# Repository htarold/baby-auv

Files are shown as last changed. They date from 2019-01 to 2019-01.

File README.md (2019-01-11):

## What
Baby AUV is a low cost, open source micro AUV (autonomous
underwater vehicle) intended for environmental monitoring
applications.  Currently it has completed basic manoeuvring and
navigation tasks, and the payload sensors (CTD) is functioning.

To move forward, the project needs a real-world problem and a
domain expert to guide further development and to take the AUV
operational.  Contact me htarold@gmail.com if you think Baby AUV
can be useful for you, or if you are interested in working on
the project.  Ideally a community can be grown to handle the
development and operational issues.

At least initially, Baby AUV should be deployed in inland waters
free of current.  Ultimately, Baby AUV will be useable in
coastal waters.

You can see a clip of Baby AUV [here](https://www.youtube.com/watch?v=7lgA8mxeRek).

## Vital statistics
Length: 0.6m (1m including antenna)
Displacement: 3.5kg
Cost: BOM cost can probably be held down to USD500.
Depth: the thruster gland has been tested to 40m; the EC probe
is rated to 50m; the hull is probably good to a few hundred
metres.
Endurance: 48 hours
Speed: 2kt (this implies range is about 100 miles)
Vehicle sensors: GPS, compass, accelerometer, depth, odometer
(via propeller)
Payload sensors: electrical conductivity, temperature.
Other payloads can be added.
Communications: RF modem (434MHz).

## How Baby AUV is different
Unlike most AUVs, Baby AUV has no fins, and has only 1 thruster,
and a moving mass actuator (2 degrees of freedom).  But by keeping
it mechanically simple and therefore cheap, it has to employ
novel methods to turn.  Gross changes of direction are achieved by
stopping, pitching nose up (by moving its internals to the rear),
then slowly reversing the thruster.  While the vehicle slowly
descends, it also rolls about a vertical axis as it reacts to the
thruster torque. At the appropriate point, the thruster is stopped
and the AUV is pitched horizontal, pointing in a new direction.

While under way, small changes in heading are achieved by modulating
the torque to the propeller which has only one blade.  This tends to
walk the rear of the AUV slowly one way or the other.  Another way
to think about this is the asymmetry of the single bladed prop
causes the AUV to wobble slightly in normal use.  By appropriately
modulating it, the wobble can be biased more one way than the other.

It should also be clear that Baby AUV is capable of hovering.

Baby AUV depends on GPS for localisation.  This means that the
AUV must surface frequently in order to get a fix.
Conveniently, for most missions the surface is very close by.

Most AUV projects are first and foremost robotics projects.
By keeping *this* AUV simple, I hope to de-emphasise the robotics
aspect in order to let the data sampling take centre stage.  In a
sense, Baby AUV can be regarded as a self-propelled multiparameter
probe, where one of the sensors s replaced by a thruster.

## Missions

The relatively high endurance and long range makes it suitable
for prolonged monitoring missions.  The AUV visits the waypoints
indicated in a mission script, collecting data along the way.
There data are stored on the SD card, and are also opportunistically
broadcast when surfaced.  If out of radio range of "home base", any
other AUV or aerial drone in the area can copy this data to return
to the user.  (A [fountain code](https://en.wikipedia.org/wiki/Fountain_code) will be used to reduce the amount
of redundant data transmitted.)  Use of such data mules make data
available sooner, as well as extending the AUV's sampling domain.

Apart from using the CTD or other payload sensor, one novel use is
to employ the AUV itself as a hydrometric pendulum.  To do this, the
AUV is trimmed slightly negative (tending to sink instead of float),
and is parked on the bottom balancing on its nose.  Any current near
the bottom (not powerful enough to dislodge the AUV) will cause
the AUV to change pitch and heading like an upside down windsock;
these are picked up by the vehicle's compass and accelerometer.
This can provide a simple way to measure the bottom shear (e.g. for
sediment transport studies), which is otherwise expensive to measure.

Baby AUV's hovering capability can be used to turn it into a
self-deploying and self-recovering fixed depth Lagrangean drifter.

Baby AUV can be used in a high surface traffic area.  The small size,
low speed, and low cost means that the AUV will sacrificially lose
in any collision with another vessel.  Conveniently, when surfaced
the AUV will be vertical, which pose softens impacts.

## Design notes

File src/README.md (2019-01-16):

Wed 16 Jan 11:07:23 +08 2019

## Source directory

Development was done on a Linux host using avr-gcc and avr-libc.
The target was flashed with the Arduino bootloader, but the
Arduino environment was not used anywhere else.  The Makefile
reflects this environment.  It's probably possible to develop on
a Windows rather than Linux host.

The binaries prefixed with `test_` are single threaded executables.
Most of them are for testing various aspects of the AUV on the
bench, including calibration.

The binaries prefixed with `tasks_` are cooperatively multitasking
executables, generally used for tank and field testing.

The multitasking consists of a simple round robin scheduler.
There are 3 hard-coded tasks: after `main()` is called, it turns
into the idle task; there is also a foreground task and a
background task.  The 3 tasks nominally take 10ms to execute in
total, the idle task soaking up any excess time to make up the
10ms.  In practice this is often the case, but nothing bad
happens if a task takes too much timer.

A task calls `yield()` to pass execution to the next task.  A
task must NOT `return`.  Extra tasks cannot be spawned, and
tasks are not allowed to die.  `yield()` can be used to delay
for approximately 10ms.

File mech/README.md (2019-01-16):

Wed 16 Jan 11:31:11 +08 2019

## Mechanical drawings

These 2D drawings were done on librecad.
I still need to properly annotate these drawings.

### `antenna.dxf`
This is for the antenna radome.  The radome contains 2 antennas
proper, for GPS and 433MHz modem.  A CNC
router (or you can use a milling machine) is used to rout out
the pocket and outline out of PVC.  Then a lathe is used to turn the
nipple, the 433MHz section, and to drill the holes for the
433MHz spring and nipple.  You may be able to get by with using
a drill press for this but it's rather dangerous.

The GPS antenna is an off-the-shelf active small ceramic patch
antenna.  The tiny screening
can over the LNA needs to be removed in order to replace the IPX
coax cable with a longer one (the can being replaced after that).
The coax cable _must be threaded_ through the antenna radome before
this is done!  Similarly for the 433MHz coax cable.  Note the
433MHz spring coax cable must be routed _behind_ the GPS antenna,
so that it lies against the screen can of the LNA, and the GPS
patch antenna must be installed facing the pocket opening.
Then the radome caps can be cemented in place with PVC cement.
You can the do the leak test.

### `baby.dxf`
Main drawing for all parts associated with the hull assembly.

The bulkhead sealing deserves a few words.  The two bulkheads take
a Neoprene ring of 5-6mm square cross section, which is compressed
against the hull by the 6 M4 screws.  This makes a water tight seal,
and also firmly attaches the bulkhead to the hull, obviating the
need for screws.  The Neoprene ring is made from a strip of the
appropriate length, by gluing the ends together in the same way
that O-rings can be made from O-ring cord.  My old source for
Neoprene strip has disappeared and I haven't looked for a new
one, but Neoprene from any source can be used.

The bulkheads themselves are turned on a lathe.  Most machining
work is concentrated here.

Small brackets are generally made from aluminium angle stock.

### `tracker.dxf`
Parts for the GPS tracker.

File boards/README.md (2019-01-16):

Wed 16 Jan 10:42:28 +08 2019

## Printed circuit boards

Baby AUV uses these PCBs.

Schematic capture and layout were done on gschem (*.sch files) and pcb
(*.pcb files) respectively, of the gEDA package.  The .tgz files
contains these, as well as the board-house-ready Gerbers.  AFAIK
these applications do not run on Windows.  The *.sch files are
NOT Eagle files.

For convenience, the *.sch.pdf (board schematics) files are also
included in the tar file.

The Makefile is only used to prepare the tgz files for upload.

### bat.{sch,pcb}
A small board to tie the 2 batteries in parallel; also
used for charging the batteries.

### encode.{sch,pcb}
This small board also doubles as the mounting for
the thruster motor.  The encoder uses an IR reflective sensor
pointed at the top surface of the shaft coupler, half of which
is coloured black with a permanent marker.  This marking must be
properly synced, so that as the prop blade rises, the encoder
outputs a rising edge, and when the blade falls, it outputs a
falling edge.

### mpx5700-pcb.{sch,pcb}
This carries the MPX5700 pressure sensor, and attaches to the
aft bulkhead.

### neo6m-hc12.{sch,pcb}
This board carries the GPS module and RF modem module, and mounts
to the foward bulkhead.  It also carries an I2C port expander to
multiplex the UARTs of both modules, as well as power them on
and off.  This board does not strictly conform to the pf-
interface.

### pf-ec.{sch,pcb}
The CTD board, which takes input from the MPX500 depth
sensor and elecrical conductivity probe.  The pf-* boards all conform
to the same IDC bus and mechanical interface.

### pf-mcu.{sch,pcb}
The MCU (ATmega328p) board.  This also carries the DC-DC
converter and servo interface (for the moving mass actuator).

### pf-thruster.{sch,pcb}
The thruster board.  This interfaces to the
thruster, which is a DC motor, and the encoder board.

### tracker-power.{sch,pcb}
This is only used in the RF tracker, not the
AUV.  It is a mounting for the battery socket, switch, and
charging board.

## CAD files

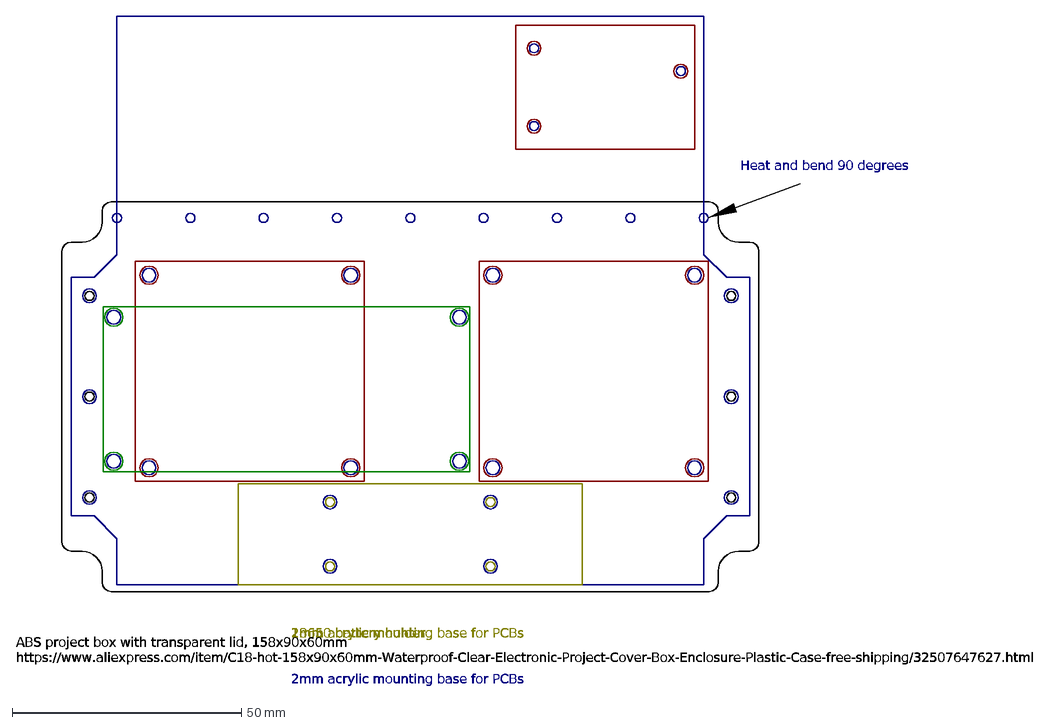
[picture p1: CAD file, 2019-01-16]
mech/tracker.dxf
18650 battery holder
2mm acrylic mounting base for PCBs
Heat and bend 90 degrees
ABS project box with transparent lid, 158x90x60mm https://www.aliexpress.com/item/C18-hot-158x90x60mm-Waterproof-Clear-Electronic-Project-Cover-Box-Enclosure-Pl

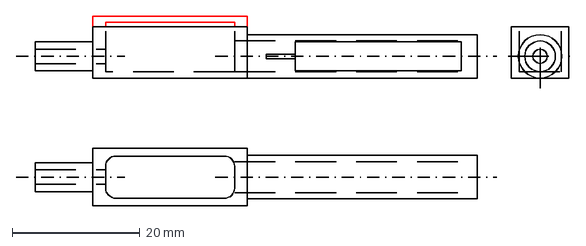
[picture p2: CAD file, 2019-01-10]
mech/antenna.dxf
86.6 x 29.7 mm

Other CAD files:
mech/baby.dxf

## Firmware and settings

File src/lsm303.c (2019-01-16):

/*
  (C) 2019 Harold Tay LGPLv3
  LSM303:
  Accel gives 12 bit values, but range is +/-2g, so 1g
  corresponds to 1024.
  Bits are LEFT aligned.

  For orientation, follow Table 2 of LSM app note:
               Ax Ay Az
  Z down       0  0  +1g
  Z up         0  0  -1g
  Y down       0 +1g 0
  Y up         0 -1g 0
  X down      +1g 0  0
  X up        -1g 0  0
  These are the axes of the AUV, XYZ are NED.  Change the
  AUVXFRONT/AUVYLEFT/AUVZUP macros in tude.h until the a[]
  values have the correct sign.

  Compass REQUIRES calibration; Z axis is generally badly off.
  Compass gain should also not be max because the values may
  overflow before applying the calibration offsets.
 */

#include <avr/eeprom.h>
#include "i2c.h"
#include "tude.h"
#include "tx.h"
#include "fmt.h"
#include "ee.h"                       /* for calibration values */

#define LSM303DLHC

#undef  DBG_LSM303
#ifdef DBG_LSM303
#define PRINT(a) a
#else
#define PRINT(a) /* nothing */
#endif

static struct tude calib;  /* contains calibration offsets */

static int8_t load_offsets(int16_t * ary, int16_t * addr)
{
  if (ee_load(ary, addr, sizeof(calib.cmpas_offsets))) {
    uint8_t i;
    for(i = 0; i < 3; i++) ary[i] = 0;
    /* is uncalibrated, calibration is REQUIRED */
    return(1);
  }
  return(0);
}

/*
  Accelerometer addresses are different for DLH and DLHC.
 */
#define ACCEL_ADDR_DLH (0x18<<1)
#define ACCEL_ADDR_DLHC (0x19<<1)
#define CMPAS_ADDR (0x1E<<1)
static uint8_t accel_addr;

static int8_t accelinit(int8_t addr)
{
  int8_t e;

  i2c_init();
  if( (e = i2c_setreg(addr, 0x20, 0x37)) )return(e);
  /* CANNOT set small/native endian, DLHC bug. */
  e = i2c_setreg(addr, 0x23, addr == ACCEL_ADDR_DLHC?0x1:0);
  return(e);
}
int8_t accel_init(void)
{
  int8_t e;
  e = accelinit(accel_addr = ACCEL_ADDR_DLH);
  if (e) e = accelinit(accel_addr = ACCEL_ADDR_DLHC);
  if (e) return(e);
  return(load_offsets(calib.accel_offsets, ee.tude.accel_offsets));
}
static void reorient(int16_t ary[3])
{
  int16_t tmp[3];
  tmp[0] = AUVXFRONT(ary);
  tmp[1] = AUVYRIGHT(ary);
  tmp[2] = AUVZDOWN(ary);

  ary[0] = tmp[0];
  ary[1] = tmp[1];
  ary[2] = tmp[2];
}
static int8_t read6(uint8_t addr, uint8_t reg, uint16_t ary[3])
{
  int i;
  uint8_t buf[6];
  i = i2c_read(addr, reg, buf, 6);
  if( i )return(i);
  for(i = 0; i < 3; i++) {
    ary[i] = (buf[(i*2)]<<8) | (buf[(i*2)+1] & 0xff);
  }
  return(0);
}

int8_t accel_read_raw(int16_t ary[3])
{
  int8_t e;
  uint16_t tmp[3];
#define AUTO_INCREMENT (1<<7)
  e = read6(accel_addr, 0x28|AUTO_INCREMENT, tmp);
  if( e )return(e);
  /* convert endian (accel only) */
  ary[0] = ((tmp[0] << 8) & 0xff00) | ((tmp[0] >> 8) & 0xff);
  ary[1] = ((tmp[1] << 8) & 0xff00) | ((tmp[1] >> 8) & 0xff);
  ary[2] = ((tmp[2] << 8) & 0xff00) | ((tmp[2] >> 8) & 0xff);
  ary[0] /= 16;
  ary[1] /= 16;
  ary[2] /= 16;
  return(0);
}

int8_t check_magnitude(uint16_t nom2, int16_t ary[3])
{
  uint16_t magnitude2;
  uint8_t i;
  magnitude2 = (ary[0]/8)*(ary[0]/8)
             + (ary[1]/8)*(ary[1]/8)
             + (ary[2]/8)*(ary[2]/8);
  if( magnitude2 > nom2 )magnitude2 -= nom2;
  else magnitude2 = nom2 - magnitude2;
  nom2 -= nom2/4;
  for(i = 0; i < 8; i++){
    if( magnitude2 >= nom2 )break;
    magnitude2 <<= 1;
  }
  return(i);
}
int8_t accel_read(int16_t ary[3])
{
  int8_t e, i;
  e = accel_read_raw(ary);
  if( e )return(e);
  for(i = 0; i < 3; i++){
    ary[i] += calib.accel_offsets[i];
  }
  reorient(ary);
#if 0
  /*
    Warn if acceleration != 1g.
    Scaled so that 1g = 1024/8 = 128
    Compare the square: should be close to 128*128 = 16384
   */
  return(check_magnitude(16384, ary));
#else
  return(0);
#endif
}

static uint8_t cmpas_xzy;

int8_t cmpas_init(void)
{
  int8_t e;
  uint8_t b;

  /*
    Compass gain max = 1<<5, min = 7<<5
   */
  i2c_init();
  PRINT(tx_puts("## setreg 1...\r\n"));
  if( (e = i2c_setreg(CMPAS_ADDR, 0x00, 0x14)) )return(e); /* 30Hz */
  PRINT(tx_puts("## setreg 2...\r\n"));
  if( (e = i2c_setreg(CMPAS_ADDR, 0x01, 7<<5)) )return(e); /* gain */
  PRINT(tx_puts("## setreg 3...\r\n"));
  if( (e = i2c_setreg(CMPAS_ADDR, 0x02, 0x00)) )return(e); /* continuous */

  b = 0;
  PRINT(tx_puts("## i2c_read...\r\n"));
  e = i2c_read(CMPAS_ADDR, 0x0f, &b, 1);  /* xyz/xzy? */
  if (e) return(e);
  cmpas_xzy = ('<' == b);
  PRINT(tx_msg("who_am_i_m: ", b));

  return
    load_offsets(calib.cmpas_offsets, ee.tude.cmpas_offsets) |
    load_offsets(calib.cmpas_scale, ee.tude.cmpas_scale);
}

int8_t cmpas_read_raw(int16_t ary[3])
{
  int8_t e;
  e = read6(CMPAS_ADDR, 0x03, (uint16_t*)ary);
  if (e) return(e);
  if (cmpas_xzy) {
    int16_t y;
    /* positions of z and y are exchanged */
    y = ary[2]; ary[2] = ary[1]; ary[1] = y;
  }
  return(0);
}
int8_t cmpas_read(int16_t ary[3])
{
  int i;
  if( (i = cmpas_read_raw(ary)) )return(i);
  for(i = 0; i < 3; i++) {
    ary[i] += calib.cmpas_offsets[i];
    ary[i] *= calib.cmpas_scale[i];
    ary[i] /= 128;  /* approx. value of scale */
  }
  reorient(ary);
  /*
    Normal magnetic field = 0.25G (269lsb at gain = 1.9) to
    0.65G (744lsb at gain = 1.9).
   */
#if 0
  return(check_magnitude(4100, ary));
#else
  return(0);
#endif
}

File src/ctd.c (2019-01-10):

#include <avr/io.h>
#include "ctd.h"
#include "ads1015.h"
#include "i2c.h"
#include <util/delay.h>

#define DEBUG
#ifdef DEBUG
#include "tx.h"
#define DBG(x) x
#else
#define DBG(x) /* nothing */
#endif

/*
  (C) 2019 Harold Tay LGPLv3
  Always uses PGA setting of 2048mV.  For MPXxxxxAP pressure
  sensor, output is 0-5V but circuitry scales this to 0-2.x
  volts.  Thermistor and conductivity cell are excited to 2.45V,
  but response will be approx. half this value, so will be
  within range.

  Sampling at 250SPS (conservative choice).

  New channel assignments: depth = AIN0, thermistor = AIN1,
  conductivity = AIN2, v_half = AIN3.
 */

struct ctd ctd;                       /* calibrations */

#define AT24_ADDR 0x50
#define CTD_DATA_START 0

/* Read or write to the eeprom */
static int8_t eeprom_io(uint8_t addr)
{
  int8_t er, i, j;
  uint8_t * p;

  p = (uint8_t *)&ctd;

  for (i = 0; i < sizeof(ctd); i++) {
    for (j = 0; ; j++) {
      if (addr & 1)
        er = i2c_read(addr&(~1), CTD_DATA_START + i, p + i, 1);
      else
        er = i2c_setreg(addr, CTD_DATA_START + i, p[i]);
      if (!er) break;
      if (j >= 10) {
        DBG(tx_msg("## eeprom_io failed ", er));
        return(er);
      }
      _delay_us(100);
    }
  }
  return(0);
}

int8_t ctd_store_eeprom(void) { return(eeprom_io(AT24_ADDR<<1)); }

int8_t ctd_load_eeprom(void) { return(eeprom_io((AT24_ADDR<<1)|1)); }

int8_t ctd_init(void)
{
  int8_t er;
  ctd_start();
  _delay_ms(50);
  er = ctd_load_eeprom();
  ctd_stop();
  return(er);
}
void ctd_start(void)
{
  DDRD |= _BV(PD5);                   /* PD5 is OC0B */
  TCCR0A = _BV(WGM01)                 /* CTC mode 2 */
         | _BV(COM0B0);               /* Toggle on match */
  TCCR0B = _BV(CS01)|_BV(CS00);       /* /64 */
#define HZ (F_CPU/64)
  /*
    Excitation frequency will alter the readings: Too high and
    duty cycle on board becomes asymmetric.  1kHz is ok.
   */
#define EXCITATION_HZ 1000L           /* Min value 490Hz */
  OCR0A = ((HZ/2)/EXCITATION_HZ)-1;   /* TOP value */
  OCR0B = 0;
}

void ctd_stop(void)
{
  /* TCCR0B = 0; XXX leave it always on */
}

#define CFG_DEF \
ADS1015_CFG_OS | ADS1015_MODE_1SHOT|ADS1115_SPS_250\
|ADS1015_COMP_REGULAR|ADS1015_COMP_ACTIVE_LOW|ADS1015_COMP_NOLATCH\
|ADS1015_COMP_NEVER|ADS1015_PGA_1024MV

/* Differential mode reduces tempco:  */
#define CFG_DEPTH (CFG_DEF | ADS1015_MUX_AIN0AIN3)
#define CFG_THERM (CFG_DEF | ADS1015_MUX_AIN1AIN3)
#define CFG_COND  (CFG_DEF | ADS1015_MUX_AIN2AIN3)

int8_t ctd_setup(uint8_t which)
{
  static uint16_t cfgs[3] = { CFG_DEPTH, CFG_COND, CFG_THERM };

  if (which > 2) return(-1);
  return ads1015_setup(CTD_ADDR, cfgs[which]);
}
int8_t ctd_read(int16_t * p)
{
  return ads1015_get(CTD_ADDR, p);
}
int8_t ctd_busy(void)
{
  uint16_t cfg;
  int8_t er;
  er = ads1015_check(CTD_ADDR, &cfg);
  if (er) return(er);
  if (cfg & ADS1015_CFG_OS) return(0); /* Is not busy */
  return(1); /* Is busy */
}

int8_t ctd_calc_depth(int16_t raw, int16_t * dp)
{
  int32_t cm;
  cm = (raw - (int32_t)ctd.depth_offset) * (ctd.depth_gain1024);
  cm /= 1024;
  *dp = (int16_t)cm;
  return(0);
}

int8_t ctd_get_depth(int16_t * dp)
{
  int8_t er;
  int16_t raw;

  er = ctd_read(&raw);
  if (!er) er = ctd_calc_depth(raw, dp);
  return(er);
}

int8_t ctd_get_resistance(uint16_t * rp)
{
  int16_t raw;
  int8_t er;
  uint32_t num, den;

  er = ctd_read(&raw);
  if (er) return(er);

  /*
    AIN1/AIN3  Assume AIN3 is at 1/2 potential = 0.9V or
    (0.9/2.048)*65536 = 28800 counts.
    AIN1 is at V = 1.8*R/(R+10k)
    or ((1.8*R/(R+10k))/2.048)*65536 counts
    = 57600 * R/(R+10k), R = counts * 10k/(57600 - counts)
    where counts is single-ended.
    i.e. raw = counts - 28800, counts = raw + 28800
    R = (raw + 28800)*10k/(57600 - raw - 28800)
    R = (raw + 28800)*10k/(28800 - raw)
   */
  num = (raw + 28800)*10000;
  den = 28800 - raw;
  *rp = num/den;
  return(0);
}

/*
  Calculate thermistor resistance without calibration.
  uint16_t should be good down to -11 degC.
 */
int8_t ctd_calc_resistance(int16_t raw, uint16_t * rp)
{
  int32_t r, den, c_raw;

  den = (int32_t)ctd.c_vcc - (int32_t)raw;
  if (!den) return(-1);
  c_raw = raw - ctd.c_gnd;
  r = ((int32_t)ctd.therm_r * c_raw)/den;
  *rp = (uint16_t)r;
  return(0);
}

/*
  Basic formula:
  R+R2 = R1*c_raw/(c_vcc - c_raw)
  where c_* are all relative to ctd.cond_c_gnd (i.e. c_vcc =
  ctd.cond_c_vcc - ctd.cond_c_gnd, etc.)
  SCALE macro is used to extract some extra resolution from
  the arithmetic.  This mostly helps in the seawater case, not
  so much if conductivity is low.  SCALE of 32 is safe.
 */
int8_t ctd_calc_conductance(int16_t raw, uint32_t * gp)
{
  int32_t r, den, c_raw;
  c_raw = (int32_t)raw - ctd.c_gnd;
  /*
    Scale by 32 if low conductance, by 64 if high conductance:
   */
#define SCALE_LOW 32L
#define SCALE_HIGH 64L
  if (raw > 1000) {
    r = (ctd.cond_r_1 * c_raw)*SCALE_LOW;
    den = (((int32_t)ctd.c_vcc - (int32_t)ctd.c_gnd) - c_raw);
    r /= den;
    r -= ctd.cond_r_2*SCALE_LOW;
    *gp = SCALE_LOW*1000000L/r;
  } else {
    r = (ctd.cond_r_1 * c_raw)*SCALE_HIGH;
    den = (((int32_t)ctd.c_vcc - (int32_t)ctd.c_gnd) - c_raw);
    r /= den;
    r -= ctd.cond_r_2*SCALE_HIGH;
    *gp = SCALE_HIGH*1000000L/r;
  }
  return(0);
}

int8_t ctd_get_conductance(uint32_t * gp)
{
  int8_t er;
  int16_t raw;

  er = ctd_read(&raw);
  if (er) return(er);

  return(ctd_calc_conductance(raw, gp));
}

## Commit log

2019-01-10 Initial commit.
    [antenna.dxf, baby.dxf, bat.sch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]
2019-01-13 Subsumed by test-i2c_scan.c
2019-01-16 Added tracker-power, README.
    [tracker-power.sch]
2019-01-16 Added tracker, README
    [tracker.dxf]
